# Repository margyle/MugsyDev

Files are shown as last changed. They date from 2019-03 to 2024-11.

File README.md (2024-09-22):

# Mugsy

This repo has been reset and refactored to contain a monorepo of all Mugsy services. 

🚧**This update is in progress and should not be considered complete at this time.** 🚧

You can find Mugsy's individual repos, CAD files, PCB files, and more at the official Org site on Github:  https://github.com/MugsyOS

## Applications

### Operator
Operator is a FastAPI application designed to manage and control Mugsys hardware devices. All GPIO control is handled by Operator to keep hardware related functionality isolated from the primary DECAF API, allowing for increased hardware compatibility.

Until this monorepo refactor is completed, you can find limited docs, and dev and in progress feature branches on the Org repo: https://github.com/MugsyOS/Operator



### DECAF

DECAF is Mugsy's primary REST API. It handles all the non-hardware related functionality like users, recipes, integrations and tons more. DECAF also manages the brewing process through communications with Operator.

DECAF works with Mugsy's local SQLite database, using [Better-SQLite-3](https://github.com/WiseLibs/better-sqlite3), and [Drizzle](https://orm.drizzle.team/docs/overview) for a comfy dev experience.



### JuneBug

Junebug is Mugsy's React frontend. Written in TypeScript, with some help from [Tailwind](https://tailwindcss.com/), [DaisyUI](https://daisyui.com/), [TanStack Query](https://tanstack.com/query/latest), and [Jotai](https://jotai.org/). 



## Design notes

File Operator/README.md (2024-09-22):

# Mugsy: Operator Middleware


**Please note that this app is not ready for prime time just yet and this Read Me likely out of date!**
## Introduction
This repository contains the source code for the Operator App, a FastAPI application designed to manage and control Mugsys hardware devices. All GPIO control is handled by Operator to keep hardware related functionality isolated from the primary DECAF api, allowing for increased hardware compatibility. 

Requests from the Mugsy frontend are sent to the DECAF API which handles all primary functionality. When a GPIO action is required, DECAF calls Operator to perform the action.

## Getting Started

### Prerequisites
Before you begin, ensure you have the following installed on your system:
- Python 3.8 or higher
- pip
- virtualenv (optional but recommended)

### Setting Up the Environment

To set up the project environment:
1. Clone the repository:
   ```bash
   git clone https://github.com/margyle/operator.git
   cd operator
   ```

2. Create and activate a virtual environment (optional but recommended):
   - For Unix/MacOs:
     ```bash
     python -m venv venv
     source venv/bin/activate
     ```
   - For Windows:
     ```cmd
     python -m venv venv
     venv\Scripts\activate
     ```

### Installing the Application

#### Development Mode
To install the application in editable mode, which is recommended for development purposes:
```bash
pip install -e .
```
This command allows you to modify the source code and see changes without reinstalling the package.

#### Production Mode
To install the application for production use:
```bash
pip install .
```
This command installs the application as a standard Python package.

## Usage

To start the FastAPI application, run:
```bash
uvicorn operator_app.app:app --reload --host 0.0.0.0 --port 8000
```
This command will start the FastAPI server with live reloading enabled.

## Tests

To run tests, run:
```bash
pytest
```

## Troubleshooting

If you are getting import errors, you may need to add your app source to the ENV, run:
```bash
export PYTHONPATH=$PYTHONPATH:/path/to/Operator/src
```
## Scale Setup

### Install Libraries
After testing numerous libs to handle the HX711 load cell amps, the best option was found to be the [Raspberry Pi HX711 C++ Library](https://github.com/endail/hx711) by Daniel Robertson (@endail on Github), and its associated Python wrappers for interacting with it from Operator. 

Installation: 
In order to use the Python wrapper we must first install the C++ library:
* In your terminal, enter: ```sudo apt-get install -y liblgpio-dev```
* If it is not available, manually build and install it: 

```
pi@raspberrypi:~ $ git clone --depth=1 https://github.com/endail/hx711
pi@raspberrypi:~ $ cd hx711
pi@raspberrypi:~/hx711 $ make && sudo make install
```

* Run `ldconfig` , it should not require any additional actions once completed.

Install Python Wrapper:
* ```pip3 install --upgrade hx711-rpi-py```

- - -

### Calibrate Scales (headless):
The easiest method to calibrate the scales without the UI is to start Operator and connect to the calibration endpoint in Postman: ws://mugsy-0.local:8000/v1/calibrate-scales/CONE_SCALE

> If you want to calibrate the mug platform, just swap out CONE_SCALE for MUG_SCALE in the endpoint’s URL.

Once connected, you will be walked through the calibration process. Here are the steps and the response formatting for each step: 

* Step 1: Request unit
  * Text: "Enter the unit you want to measure the object in (e.g., g, kg, lb, oz):"
  * Asking: The unit of measurement for the object. Mugsy is set up to work with grams, so enter g.
  * Expected response: ```{"unit": “g”}```
* Step 2: Request known weight
  * Text: "Enter the weight of the object in [unit]:"
  * Asking: The weight of the object you are using to calibrate the scale in grams. It currently expects a float so you should enter the weight to two decimal spots.
  * Expected response: ```{"known_weight": 100.00}```
* Step 3: Request number of samples
  * Text: "Enter the number of samples to take from the HX711 chip (e.g., 15):"
  * Asking: The number of samples to take from the HX711 chip. We have had great results with a total of 15 samples.
  * Expected response: ```{"samples": 15}```
* Step 4: Zero the scale
  * Text: "Remove all objects from the scale and then press enter."
  * Asking: Confirmation that all objects have been removed from the scale
  * Expected response: ```{“ready”: true}```
* Step 5: Measure known weight
  * Text: "Place the object on the scale and then press enter."
  * Asking: Confirmation that the object has been placed on the scale
  * Expected response: ```{“ready”: true}```
 
After these steps, the endpoint sends a final JSON response with the calibration results, including:
* known_weight
* unit
* raw_value
* samples
* reference_unit
* zero_value

The calibration values are automatically written to the hardware configuration file, ready to be used in any weight related functions.

## Contributing
Contributions to this project are welcome. Please ensure that all pull requests are well-documented and include tests where applicable.

## Third-Party Libraries

### Modified Library File

The file `src/operator_services/libs/hx711.py` in this project was based on [HX711](https://github.com/gandalf15/HX711) which is licensed under the BSD 3-Clause License, Copyright (c) 2017, Marcel Zak. Modifications were made to make it compatible with pigpio.

Original Library License: [BSD 3-Clause License](https://opensource.org/licenses/BSD-3-Clause)

Please refer to the original source for the unmodified version and further details about the library.

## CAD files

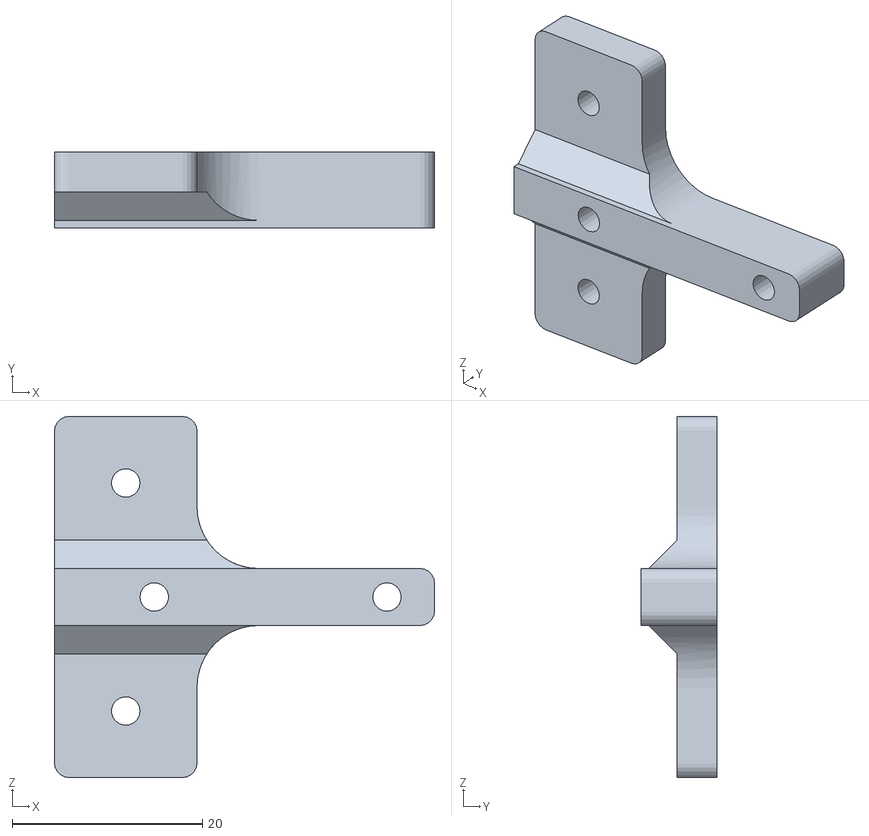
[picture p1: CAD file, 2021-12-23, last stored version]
CAD/lightbarMountRear.stl
40.0 x 8.00 x 38.0

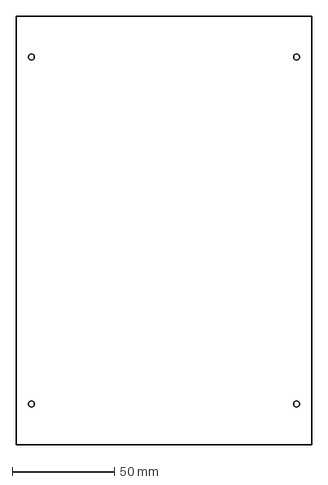
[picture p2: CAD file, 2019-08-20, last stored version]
CAD/sidePanels/mugsyBaseSidePanel_210mm.dxf
145.0 x 210.0 mm

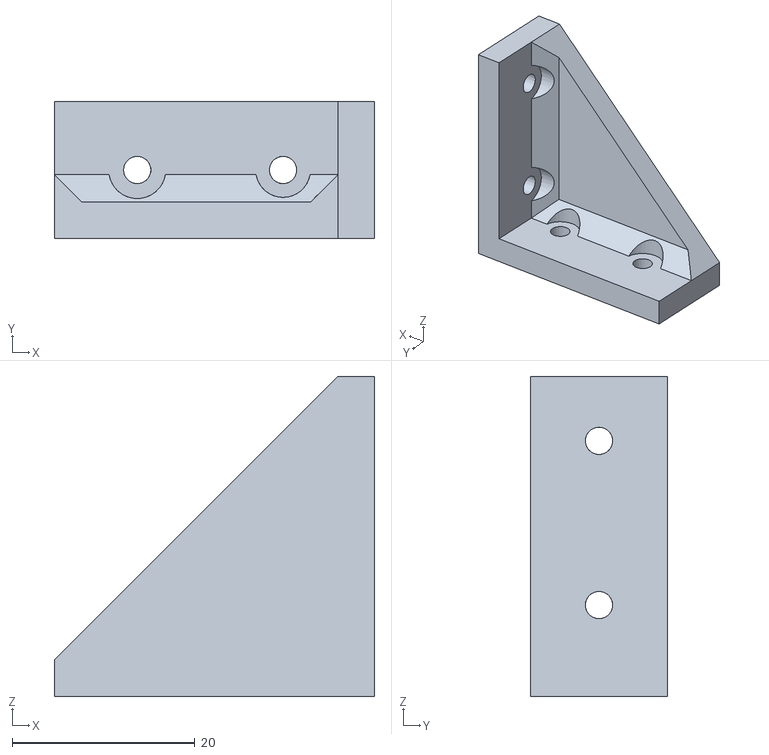
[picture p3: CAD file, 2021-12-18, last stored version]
CAD/cornerBracketV5reinforced.stl
35.0 x 15.0 x 35.0

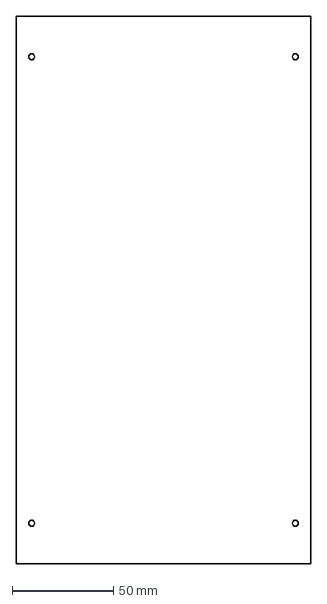
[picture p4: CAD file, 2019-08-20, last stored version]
CAD/sidePanels/mugsyBaseSidePanel_270mm.dxf
145.0 x 270.0 mm

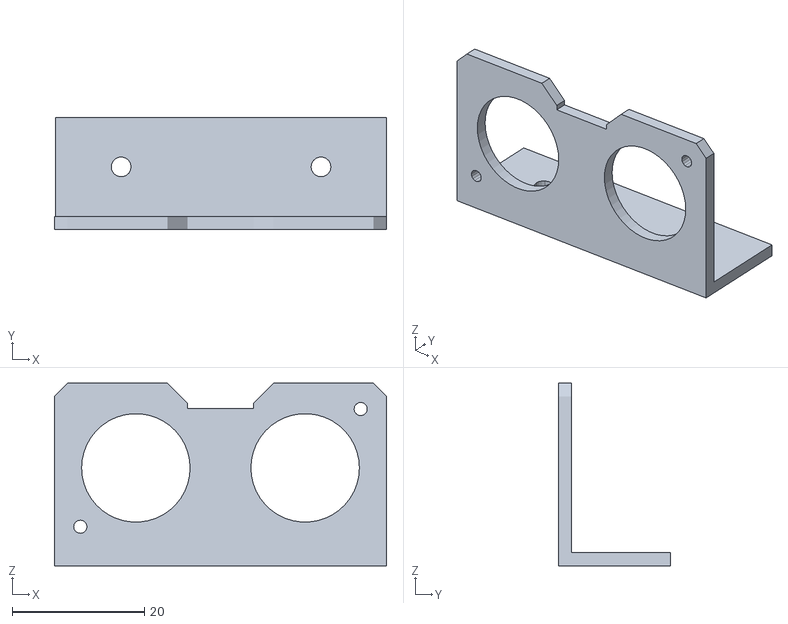
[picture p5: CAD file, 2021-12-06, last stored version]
CAD/mugSensorMount_partA.stl
50.2 x 17.0 x 27.6

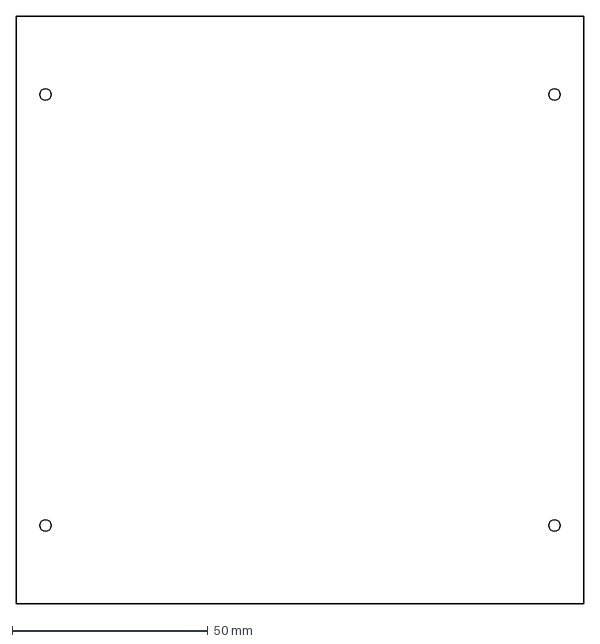
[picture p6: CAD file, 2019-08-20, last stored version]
CAD/sidePanels/mugsyBaseSidePanel.dxf
145.0 x 150.0 mm

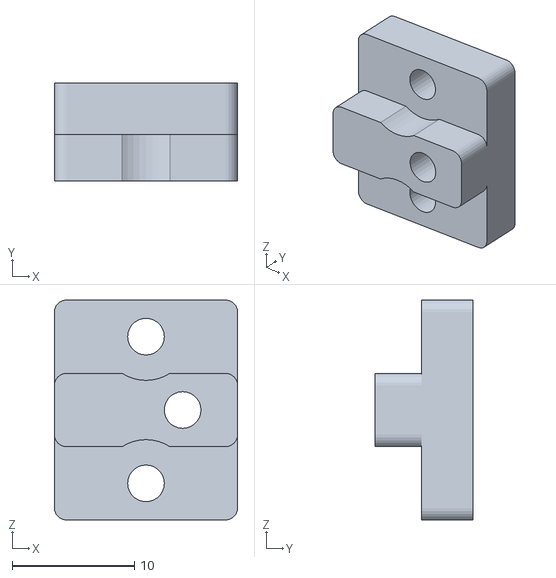
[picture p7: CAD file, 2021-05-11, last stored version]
CAD/lightBarMount_V2.stl
15.0 x 8.00 x 18.0

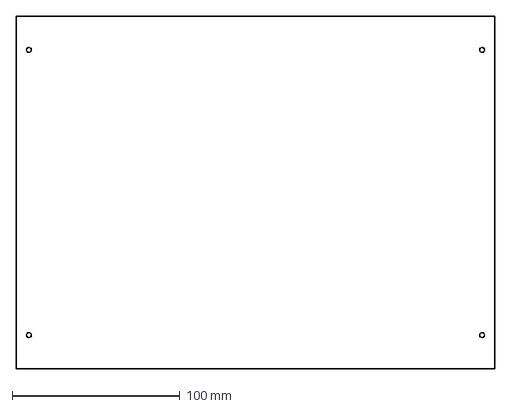
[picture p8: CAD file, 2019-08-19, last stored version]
CAD/sidePanels/mugsyHeadSidePanel.dxf
285.0 x 210.0 mm

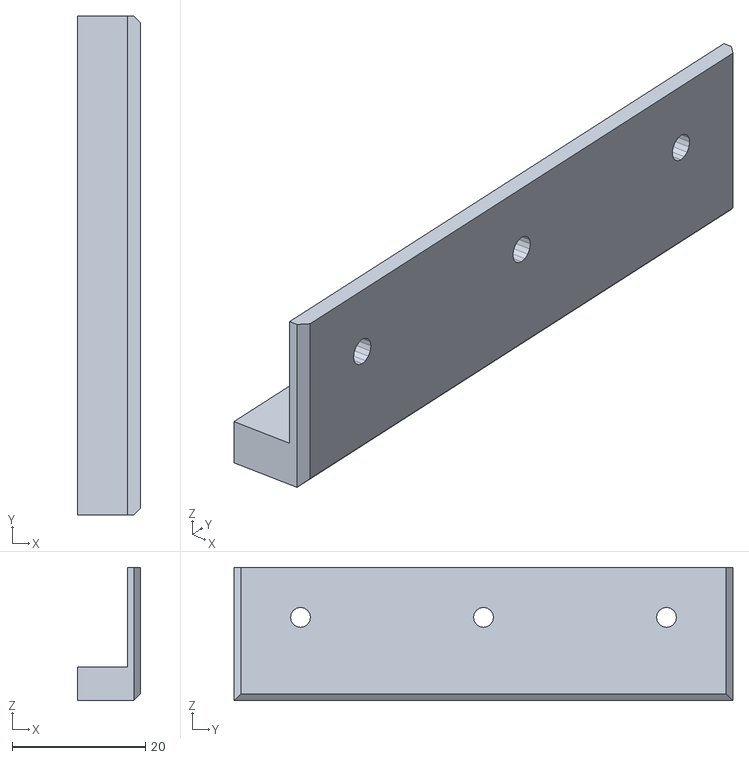
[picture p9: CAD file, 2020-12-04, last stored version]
CAD/flexBlock.stl
9.50 x 75.0 x 20.0

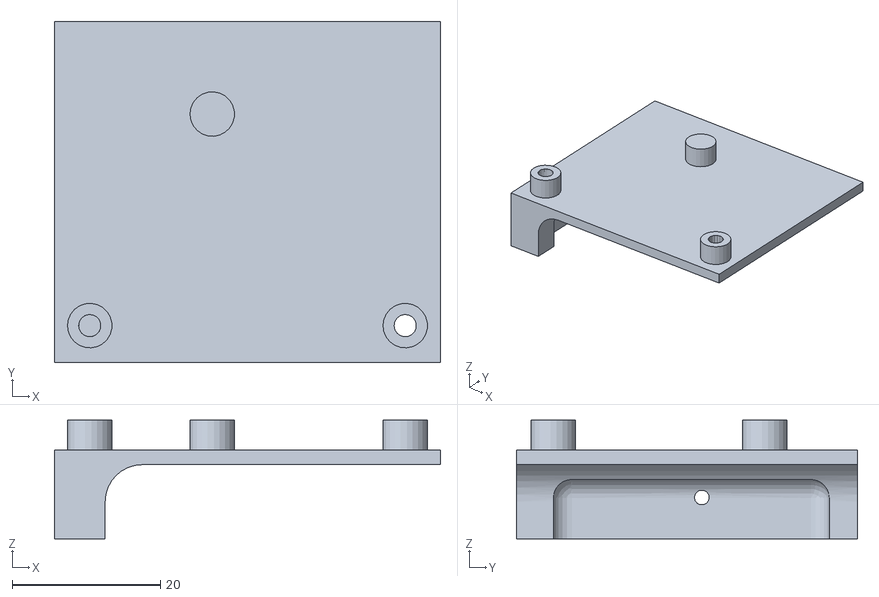
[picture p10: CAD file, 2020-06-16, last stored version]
CAD/scannerServoMount(optional).stl
52.0 x 46.0 x 16.0

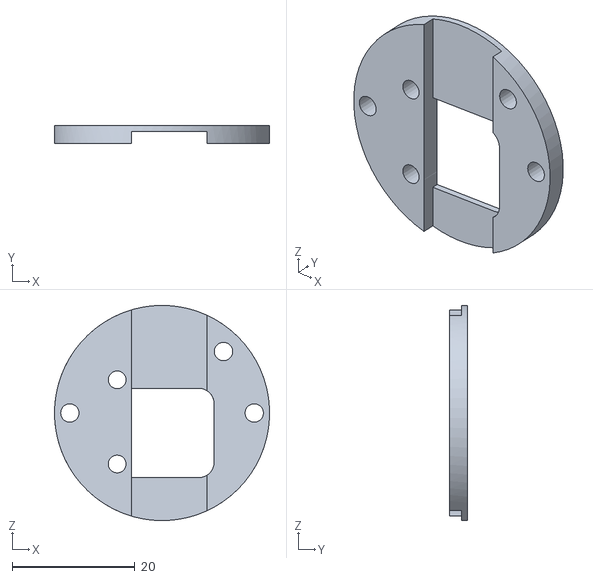
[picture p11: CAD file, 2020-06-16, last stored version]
CAD/rotaryEncoderMount.stl
35.0 x 3.00 x 35.0

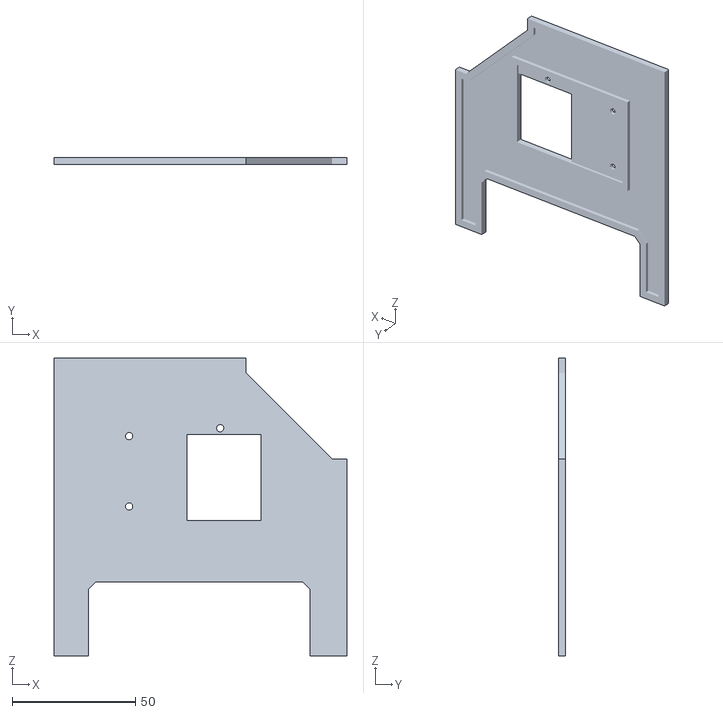
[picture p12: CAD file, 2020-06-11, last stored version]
CAD/rfidMount_V3.stl
119.0 x 3.00 x 121.0

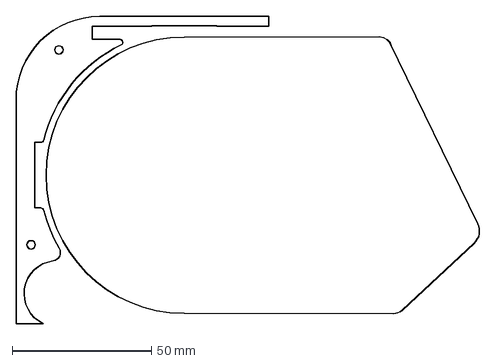
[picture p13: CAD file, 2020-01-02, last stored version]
CAD/mugsyBelt.dxf
167.0 x 110.3 mm

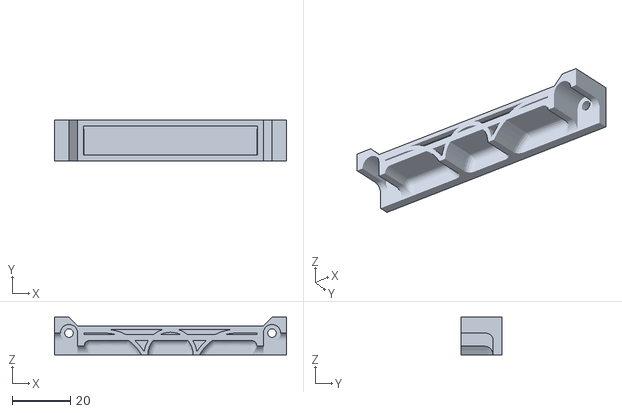
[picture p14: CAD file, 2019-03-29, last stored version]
CAD/panelMagnetMount.V4.stl
80.0 x 14.0 x 13.0

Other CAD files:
CAD/magConnPanelSide.2.stl
CAD/magConnLid.2.stl
CAD/magConnMachineSide.2.stl
CAD/plugCap.stl
CAD/PouroverMidSection.stl
CAD/barcodeScanMount.stl
CAD/behindScreenDividerLaser.dxf
CAD/coneMechGear.stl
CAD/coneMechGearTop.stl
CAD/coneMechMid.stl
CAD/controllerPlates.stl
CAD/controllerPlatesLaser.dxf
CAD/grinderGear.stl
CAD/grinderSpoutMountV2.stl
CAD/grinderSpoutV2.stl
CAD/pourOverMechTop.dxf
CAD/pourOverMount.stl
CAD/rgbLedMount.stl
CAD/screenClipV2.stl
CAD/sweepServoMount.stl
CAD/waterSweepV1.stl

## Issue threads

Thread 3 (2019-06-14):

nonBlockingSerialStepper.ino broke command chaining

margyle, 2019-06-14:
Move to non-blocking motor controller introduced some bugs.  Most important one being command chaining. Fix in progress.

margyle, 2019-06-14:
Fixed the command chaining bug. Just need to reintegrate the water pump control, come clean up and we are good to go.

Closed 2019-06-22.

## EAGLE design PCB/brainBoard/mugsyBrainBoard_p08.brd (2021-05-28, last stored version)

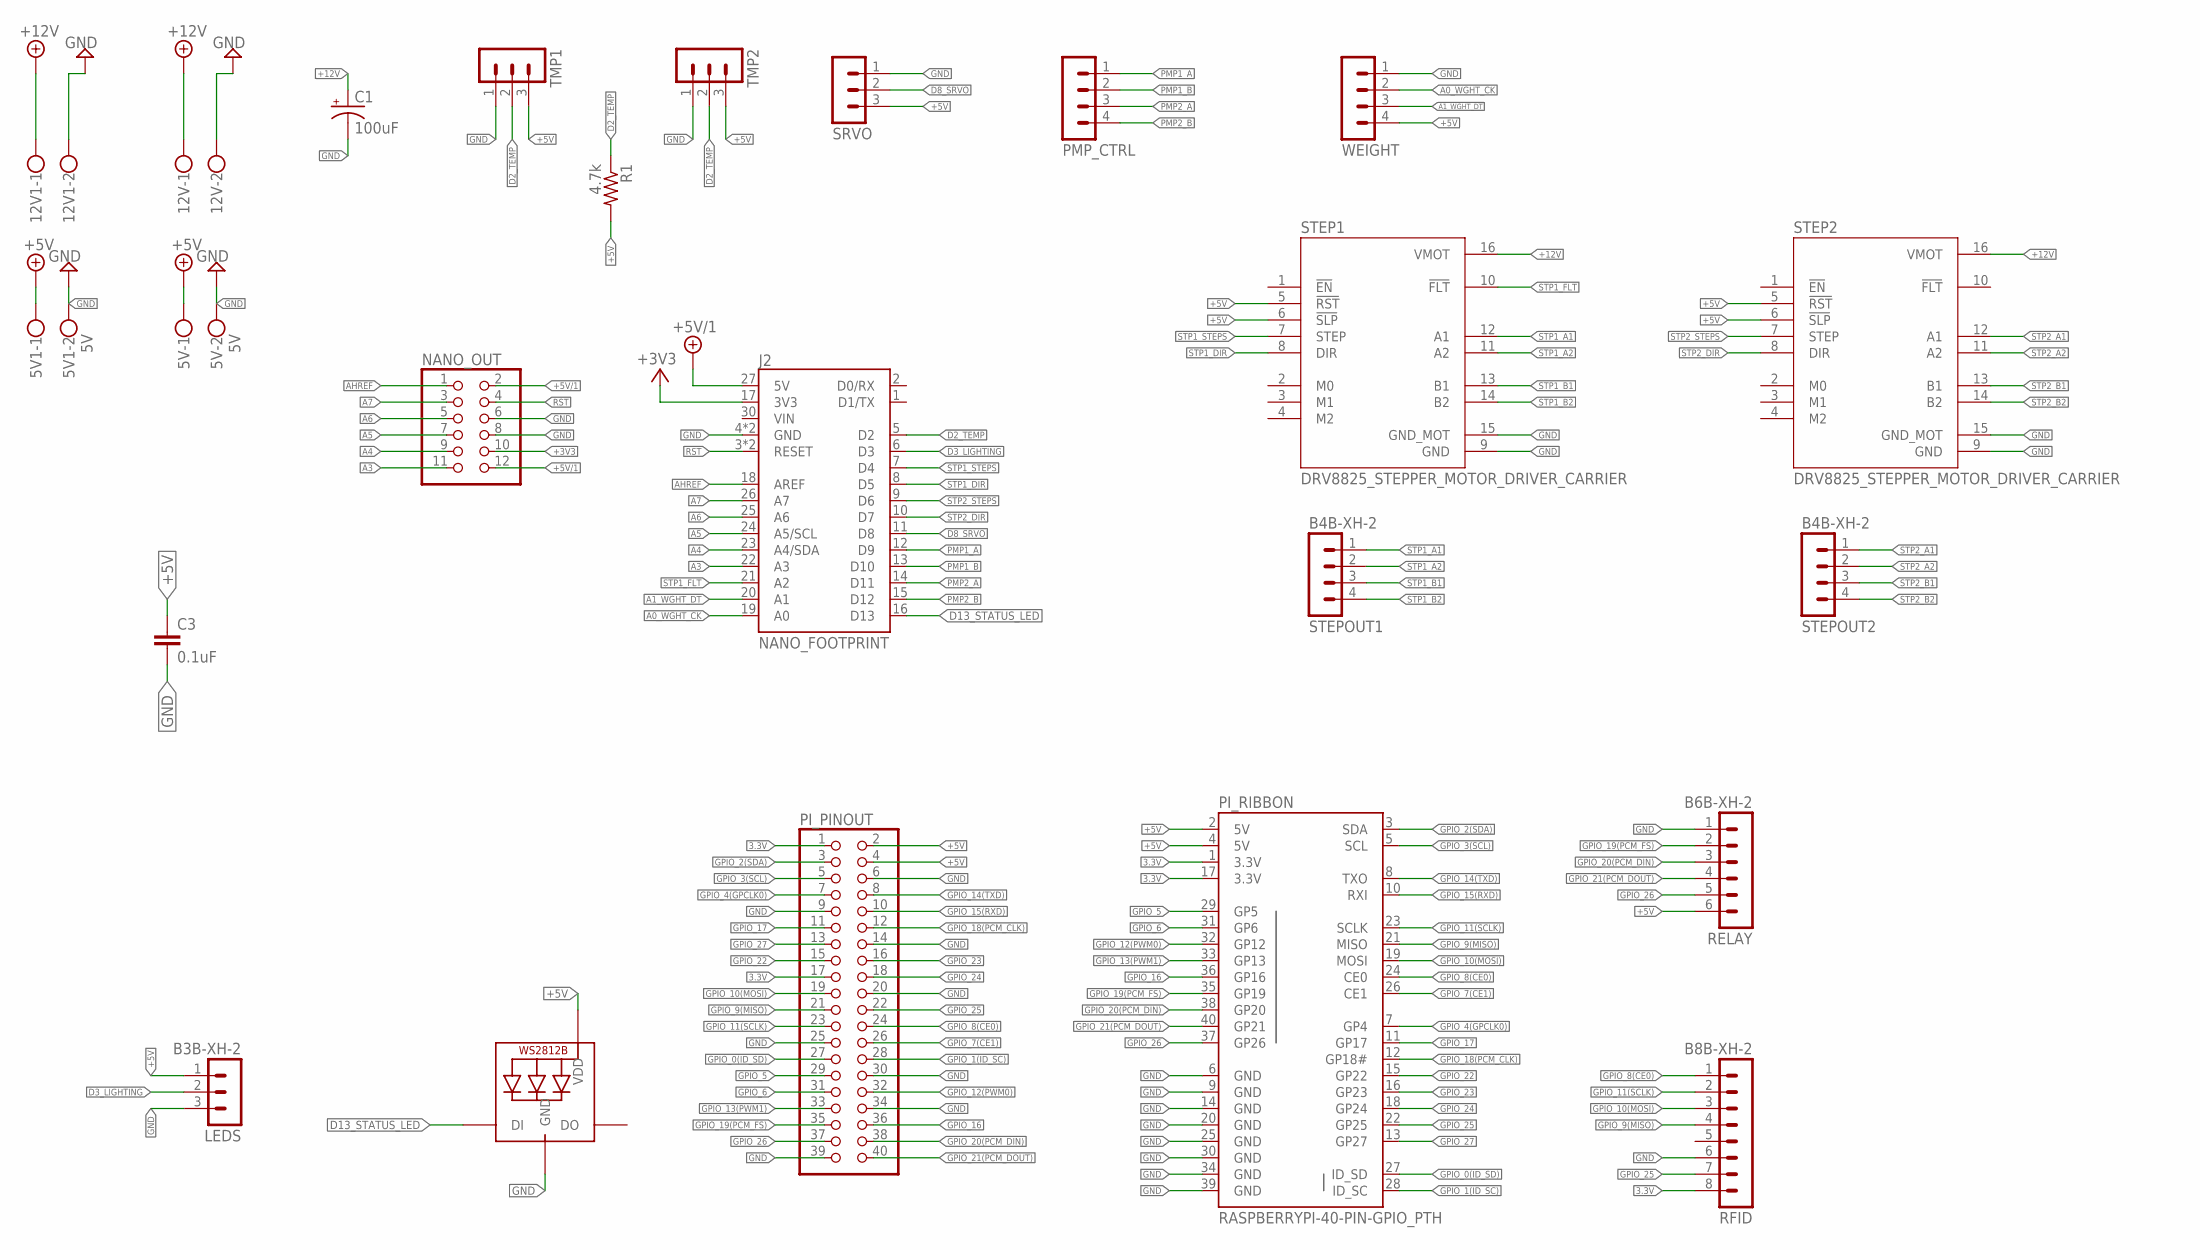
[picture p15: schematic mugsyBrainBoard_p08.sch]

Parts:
5V, 5V1: 5V; W237-102
12V, 12V1: W237-102
C1: 100uF; CPOL-RADIAL-2.5MM-6.5MM
C3: 0.1uF; C050-030X075
J2: NANO_FOOTPRINT; NANO
LEDS: B3B-XH-2; B3B-XH-A
NANO_OUT: PINHD-2X6; 2X06
PI_PINOUT: PINHD-2X20; 2X20
PI_RIBBON: RASPBERRYPI-40-PIN-GPIO_PTH; 2X20_SHROUDED
PMP_CTRL: B4B-XH-2; B4B-XH-A
R1: 4.7k; 0207/5V
RELAY: B6B-XH-2; B6B-XH-A
RFID: B8B-XH-2; B8B-XH-A
SRVO: B3B-XH-2; B3B-XH-A
STATUS: WS2812B5050; WS2812B
STEP1, STEP2: DRV8825_STEPPER_MOTOR_DRIVER_CARRIER; IC_DRV8825_STEPPER_MOTOR_DRIVER_CARRIER
STEPOUT1, STEPOUT2: B4B-XH-2; B4B-XH-A
TMP1, TMP2: B3B-XH-2; B3B-XH-A
WEIGHT: B4B-XH-2; B4B-XH-A

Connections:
3.3V: PI_PINOUT.1, PI_PINOUT.17, PI_RIBBON.1 (3.3V), PI_RIBBON.17 (3.3V), RFID.8
+3V3: J2.17 (3V3), NANO_OUT.10
+5V: 5V.1, 5V1.1, C3.1, LEDS.1, PI_PINOUT.2, PI_PINOUT.4, PI_RIBBON.2 (5V), PI_RIBBON.4 (5V), R1.2, RELAY.6, SRVO.3, STATUS.1-VDD (VDD), STEP1.5 (!RST), STEP1.6 (!SLP), STEP2.5 (!RST), STEP2.6 (!SLP), TMP1.3, TMP2.3, WEIGHT.4
+5V/1: J2.27 (5V), NANO_OUT.2, NANO_OUT.12
+12V: 12V.1, 12V1.1, C1.1 (+), STEP1.16 (VMOT), STEP2.16 (VMOT)
A0_WGHT_CK: J2.19 (A0), WEIGHT.2
A1_WGHT_DT: J2.20 (A1), WEIGHT.3
A3: J2.22 (A3), NANO_OUT.11
A4: J2.23 (A4/SDA), NANO_OUT.9
A5: J2.24 (A5/SCL), NANO_OUT.7
A6: J2.25 (A6), NANO_OUT.5
A7: J2.26 (A7), NANO_OUT.3
AHREF: J2.18 (AREF), NANO_OUT.1
D2_TEMP: J2.5 (D2), R1.1, TMP1.2, TMP2.2
D3_LIGHTING: J2.6 (D3), LEDS.2
D8_SRVO: J2.11 (D8), SRVO.2
D13_STATUS_LED: J2.16 (D13), STATUS.4-DIN (DI)
GND: 5V.2, 5V1.2, 12V.2, 12V1.2, C1.2 (-), C3.2, J2.4 (GND), J2.29 (GND), LEDS.3, NANO_OUT.6, NANO_OUT.8, PI_PINOUT.6, PI_PINOUT.9, PI_PINOUT.14, PI_PINOUT.20, PI_PINOUT.25, PI_PINOUT.30, PI_PINOUT.34, PI_PINOUT.39, PI_RIBBON.6 (GND), PI_RIBBON.9 (GND), PI_RIBBON.14 (GND), PI_RIBBON.20 (GND), PI_RIBBON.25 (GND), PI_RIBBON.30 (GND), PI_RIBBON.34 (GND), PI_RIBBON.39 (GND), RELAY.1, RFID.6, SRVO.1, STATUS.3-GND (GND), STEP1.9 (GND), STEP1.15 (GND_MOT), STEP2.9 (GND), STEP2.15 (GND_MOT), TMP1.1, TMP2.1, WEIGHT.1
GPIO_0(ID_SD): PI_PINOUT.27, PI_RIBBON.27 (ID_SD)
GPIO_1(ID_SC): PI_PINOUT.28, PI_RIBBON.28 (ID_SC)
GPIO_2(SDA): PI_PINOUT.3, PI_RIBBON.3 (SDA)
GPIO_3(SCL): PI_PINOUT.5, PI_RIBBON.5 (SCL)
GPIO_4(GPCLK0): PI_PINOUT.7, PI_RIBBON.7 (GP4)
GPIO_5: PI_PINOUT.29, PI_RIBBON.29 (GP5)
GPIO_6: PI_PINOUT.31, PI_RIBBON.31 (GP6)
GPIO_7(CE1): PI_PINOUT.26, PI_RIBBON.26 (CE1)
GPIO_8(CE0): PI_PINOUT.24, PI_RIBBON.24 (CE0), RFID.1
GPIO_9(MISO): PI_PINOUT.21, PI_RIBBON.21 (MISO), RFID.4
GPIO_10(MOSI): PI_PINOUT.19, PI_RIBBON.19 (MOSI), RFID.3
GPIO_11(SCLK): PI_PINOUT.23, PI_RIBBON.23 (SCLK), RFID.2
GPIO_12(PWM0): PI_PINOUT.32, PI_RIBBON.32 (GP12)
GPIO_13(PWM1): PI_PINOUT.33, PI_RIBBON.33 (GP13)
GPIO_14(TXD): PI_PINOUT.8, PI_RIBBON.8 (TXO)
GPIO_15(RXD): PI_PINOUT.10, PI_RIBBON.10 (RXI)
GPIO_16: PI_PINOUT.36, PI_RIBBON.36 (GP16)
GPIO_17: PI_PINOUT.11, PI_RIBBON.11 (GP17)
GPIO_18(PCM_CLK): PI_PINOUT.12, PI_RIBBON.12 (GP18#)
GPIO_19(PCM_FS): PI_PINOUT.35, PI_RIBBON.35 (GP19), RELAY.2
GPIO_20(PCM_DIN): PI_PINOUT.38, PI_RIBBON.38 (GP20), RELAY.3
GPIO_21(PCM_DOUT): PI_PINOUT.40, PI_RIBBON.40 (GP21), RELAY.4
GPIO_22: PI_PINOUT.15, PI_RIBBON.15 (GP22)
GPIO_23: PI_PINOUT.16, PI_RIBBON.16 (GP23)
GPIO_24: PI_PINOUT.18, PI_RIBBON.18 (GP24)
GPIO_25: PI_PINOUT.22, PI_RIBBON.22 (GP25), RFID.7
GPIO_26: PI_PINOUT.37, PI_RIBBON.37 (GP26), RELAY.5
GPIO_27: PI_PINOUT.13, PI_RIBBON.13 (GP27)
PMP1_A: J2.12 (D9), PMP_CTRL.1
PMP1_B: J2.13 (D10), PMP_CTRL.2
PMP2_A: J2.14 (D11), PMP_CTRL.3
PMP2_B: J2.15 (D12), PMP_CTRL.4
RST: J2.3 (RESET), J2.28 (RESET), NANO_OUT.4
STP1_A1: STEP1.12 (A1), STEPOUT1.1
STP1_A2: STEP1.11 (A2), STEPOUT1.2
STP1_B1: STEP1.13 (B1), STEPOUT1.3
STP1_B2: STEP1.14 (B2), STEPOUT1.4
STP1_DIR: J2.8 (D5), STEP1.8 (DIR)
STP1_FLT: J2.21 (A2), STEP1.10 (!FLT)
STP1_STEPS: J2.7 (D4), STEP1.7 (STEP)
STP2_A1: STEP2.12 (A1), STEPOUT2.1
STP2_A2: STEP2.11 (A2), STEPOUT2.2
STP2_B1: STEP2.13 (B1), STEPOUT2.3
STP2_B2: STEP2.14 (B2), STEPOUT2.4
STP2_DIR: J2.10 (D7), STEP2.8 (DIR)
STP2_STEPS: J2.9 (D6), STEP2.7 (STEP)

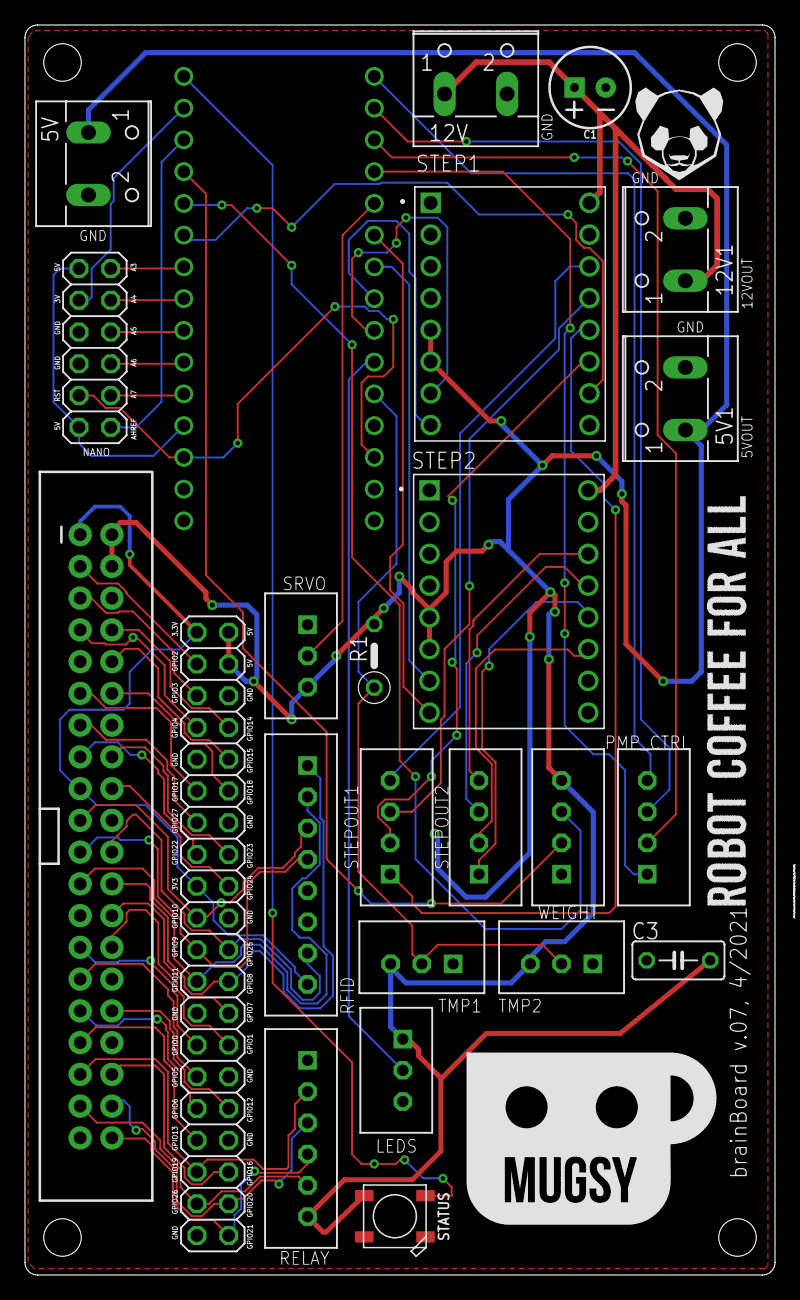
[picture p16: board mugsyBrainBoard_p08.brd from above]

Board: 2 copper layers, 60.0 x 100.0 mm, 24 parts (0 on the bottom side), 64 nets.

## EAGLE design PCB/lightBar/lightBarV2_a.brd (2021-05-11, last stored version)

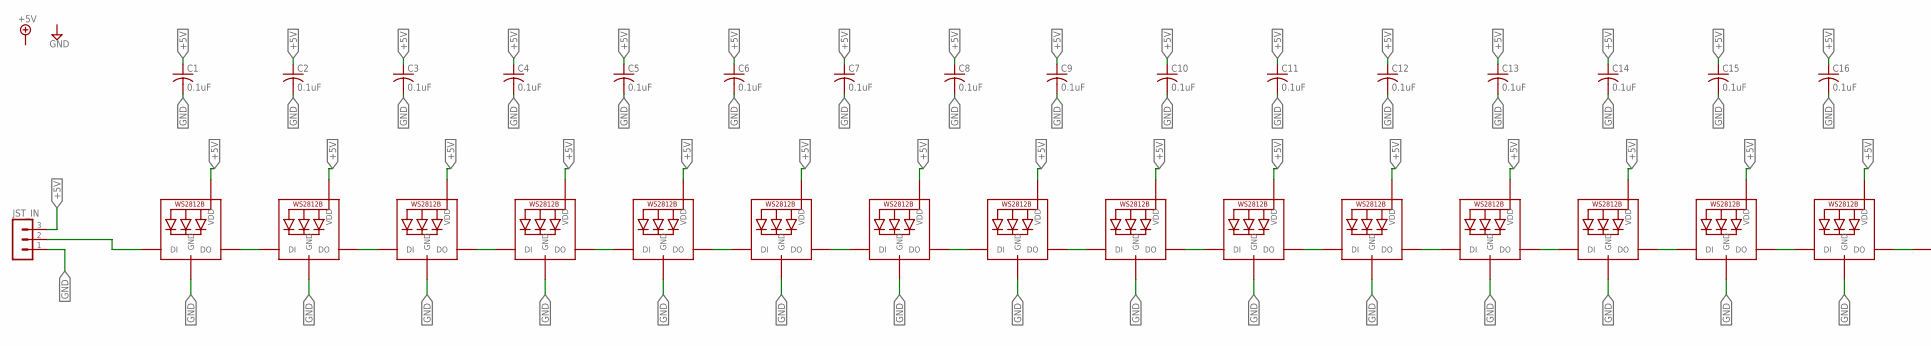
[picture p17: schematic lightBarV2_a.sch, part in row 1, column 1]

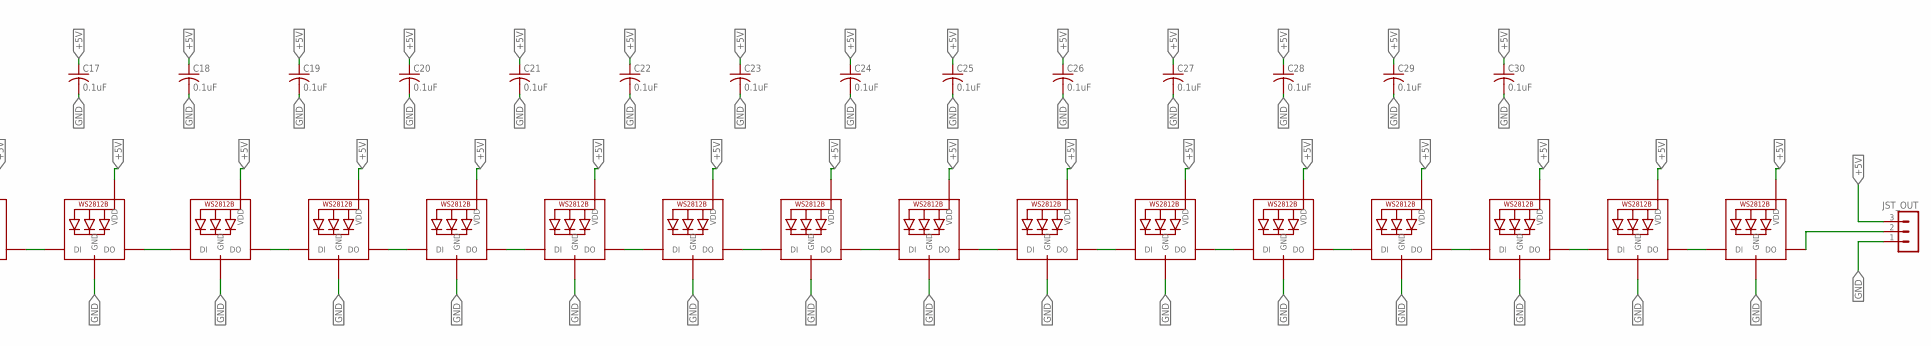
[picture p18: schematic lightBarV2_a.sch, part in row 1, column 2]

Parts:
C1, C2, C3, C4, C5, C6, C7, C8, C9, C10, C11, C12, C13, C14, C15, C16, C17, C18, C19, C20, C21, C22, C23, C24, C25, C26, C27, C28, C29, C30: 0.1uF; C0805K
JST_IN: B3B-XH-2; B3B-XH-A
JST_OUT: B3B-XH-2; B3B-XH-A
LED1, LED2, LED3, LED4, LED5, LED6, LED7, LED8, LED9, LED10, LED11, LED12, LED13, LED14, LED15, LED16, LED17, LED18, LED19, LED20, LED21, LED22, LED23, LED24, LED25, LED26, LED27, LED28, LED29, LED30: WS2812B5050; WS2812B

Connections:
+5V: C1.1, C2.1, C3.1, C4.1, C5.1, C6.1, C7.1, C8.1, C9.1, C10.1, C11.1, C12.1, C13.1, C14.1, C15.1, C16.1, C17.1, C18.1, C19.1, C20.1, C21.1, C22.1, C23.1, C24.1, C25.1, C26.1, C27.1, C28.1, C29.1, C30.1, JST_IN.3, JST_OUT.3, LED1.1-VDD (VDD), LED2.1-VDD (VDD), LED3.1-VDD (VDD), LED4.1-VDD (VDD), LED5.1-VDD (VDD), LED6.1-VDD (VDD), LED7.1-VDD (VDD), LED8.1-VDD (VDD), LED9.1-VDD (VDD), LED10.1-VDD (VDD), LED11.1-VDD (VDD), LED12.1-VDD (VDD), LED13.1-VDD (VDD), LED14.1-VDD (VDD), LED15.1-VDD (VDD), LED16.1-VDD (VDD), LED17.1-VDD (VDD), LED18.1-VDD (VDD), LED19.1-VDD (VDD), LED20.1-VDD (VDD), LED21.1-VDD (VDD), LED22.1-VDD (VDD), LED23.1-VDD (VDD), LED24.1-VDD (VDD), LED25.1-VDD (VDD), LED26.1-VDD (VDD), LED27.1-VDD (VDD), LED28.1-VDD (VDD), LED29.1-VDD (VDD), LED30.1-VDD (VDD)
GND: C1.2, C2.2, C3.2, C4.2, C5.2, C6.2, C7.2, C8.2, C9.2, C10.2, C11.2, C12.2, C13.2, C14.2, C15.2, C16.2, C17.2, C18.2, C19.2, C20.2, C21.2, C22.2, C23.2, C24.2, C25.2, C26.2, C27.2, C28.2, C29.2, C30.2, JST_IN.1, JST_OUT.1, LED1.3-GND (GND), LED2.3-GND (GND), LED3.3-GND (GND), LED4.3-GND (GND), LED5.3-GND (GND), LED6.3-GND (GND), LED7.3-GND (GND), LED8.3-GND (GND), LED9.3-GND (GND), LED10.3-GND (GND), LED11.3-GND (GND), LED12.3-GND (GND), LED13.3-GND (GND), LED14.3-GND (GND), LED15.3-GND (GND), LED16.3-GND (GND), LED17.3-GND (GND), LED18.3-GND (GND), LED19.3-GND (GND), LED20.3-GND (GND), LED21.3-GND (GND), LED22.3-GND (GND), LED23.3-GND (GND), LED24.3-GND (GND), LED25.3-GND (GND), LED26.3-GND (GND), LED27.3-GND (GND), LED28.3-GND (GND), LED29.3-GND (GND), LED30.3-GND (GND)
unnamed: LED29.2-DOUT (DO), LED30.4-DIN (DI)
unnamed: LED28.2-DOUT (DO), LED29.4-DIN (DI)
unnamed: LED27.2-DOUT (DO), LED28.4-DIN (DI)
unnamed: LED26.2-DOUT (DO), LED27.4-DIN (DI)
unnamed: LED25.2-DOUT (DO), LED26.4-DIN (DI)
unnamed: LED24.2-DOUT (DO), LED25.4-DIN (DI)
unnamed: LED23.2-DOUT (DO), LED24.4-DIN (DI)
unnamed: LED22.2-DOUT (DO), LED23.4-DIN (DI)
unnamed: LED21.2-DOUT (DO), LED22.4-DIN (DI)
unnamed: LED20.2-DOUT (DO), LED21.4-DIN (DI)
unnamed: LED19.2-DOUT (DO), LED20.4-DIN (DI)
unnamed: LED18.2-DOUT (DO), LED19.4-DIN (DI)
unnamed: LED17.2-DOUT (DO), LED18.4-DIN (DI)
unnamed: LED16.2-DOUT (DO), LED17.4-DIN (DI)
unnamed: LED15.2-DOUT (DO), LED16.4-DIN (DI)
unnamed: LED14.2-DOUT (DO), LED15.4-DIN (DI)
unnamed: LED13.2-DOUT (DO), LED14.4-DIN (DI)
unnamed: LED12.2-DOUT (DO), LED13.4-DIN (DI)
unnamed: LED11.2-DOUT (DO), LED12.4-DIN (DI)
unnamed: LED10.2-DOUT (DO), LED11.4-DIN (DI)
unnamed: LED9.2-DOUT (DO), LED10.4-DIN (DI)
unnamed: LED8.2-DOUT (DO), LED9.4-DIN (DI)
unnamed: LED7.2-DOUT (DO), LED8.4-DIN (DI)
unnamed: LED6.2-DOUT (DO), LED7.4-DIN (DI)
unnamed: LED5.2-DOUT (DO), LED6.4-DIN (DI)
unnamed: LED4.2-DOUT (DO), LED5.4-DIN (DI)
unnamed: LED3.2-DOUT (DO), LED4.4-DIN (DI)
unnamed: LED1.2-DOUT (DO), LED2.4-DIN (DI)
unnamed: LED2.2-DOUT (DO), LED3.4-DIN (DI)
unnamed: JST_IN.2, LED1.4-DIN (DI)
unnamed: JST_OUT.2, LED30.2-DOUT (DO)

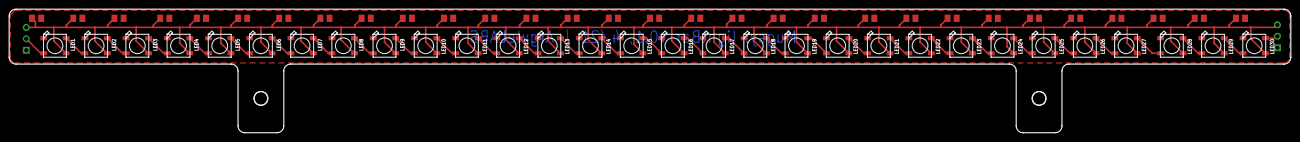
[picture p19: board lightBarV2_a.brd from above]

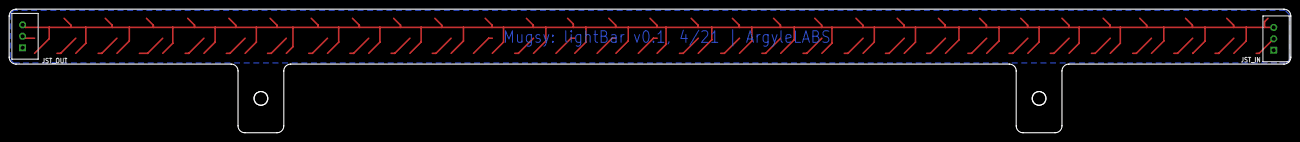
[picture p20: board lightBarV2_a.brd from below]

Board: 2 copper layers, 280.0 x 27.0 mm, 62 parts (2 on the bottom side), 33 nets.

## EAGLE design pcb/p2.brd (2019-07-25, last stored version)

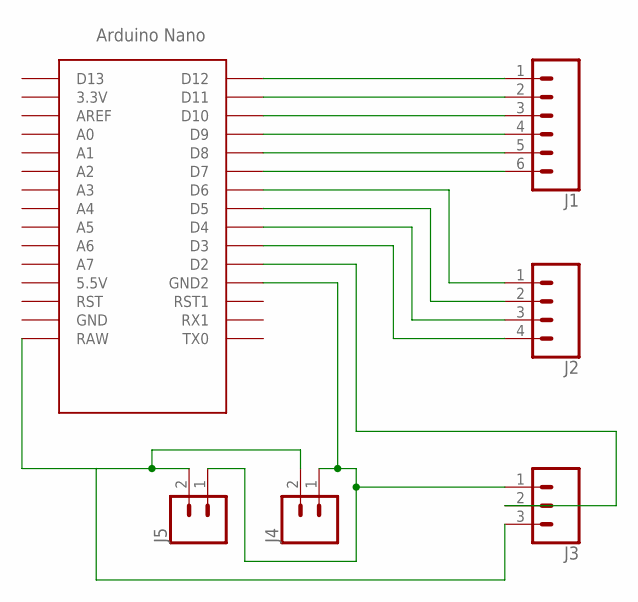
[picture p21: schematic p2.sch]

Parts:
J1: CONN_06LONGPADS; 1X06_LONGPADS
J2: CONN_04LONGPADS; 1X04_LONGPADS
J3: CONN_03LONGPADS; 1X03_LONGPADS
J4, J5: CONN_02PTH3; 1X02_LONGPADS
U$1: NANO

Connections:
unnamed: J1.1, U$1.D12
unnamed: J1.2, U$1.D11
unnamed: J1.3, U$1.D10
unnamed: J1.4, U$1.D9
unnamed: J1.5, U$1.D8
unnamed: J1.6, U$1.D7
unnamed: J2.1, U$1.D6
unnamed: J2.2, U$1.D5
unnamed: J2.3, U$1.D4
unnamed: J2.4, U$1.D3
unnamed: J3.2, U$1.D2
unnamed: J3.3, J4.2, J5.2, U$1.RAW
unnamed: J3.1, J4.1, J5.1, U$1.GND1 (GND2)

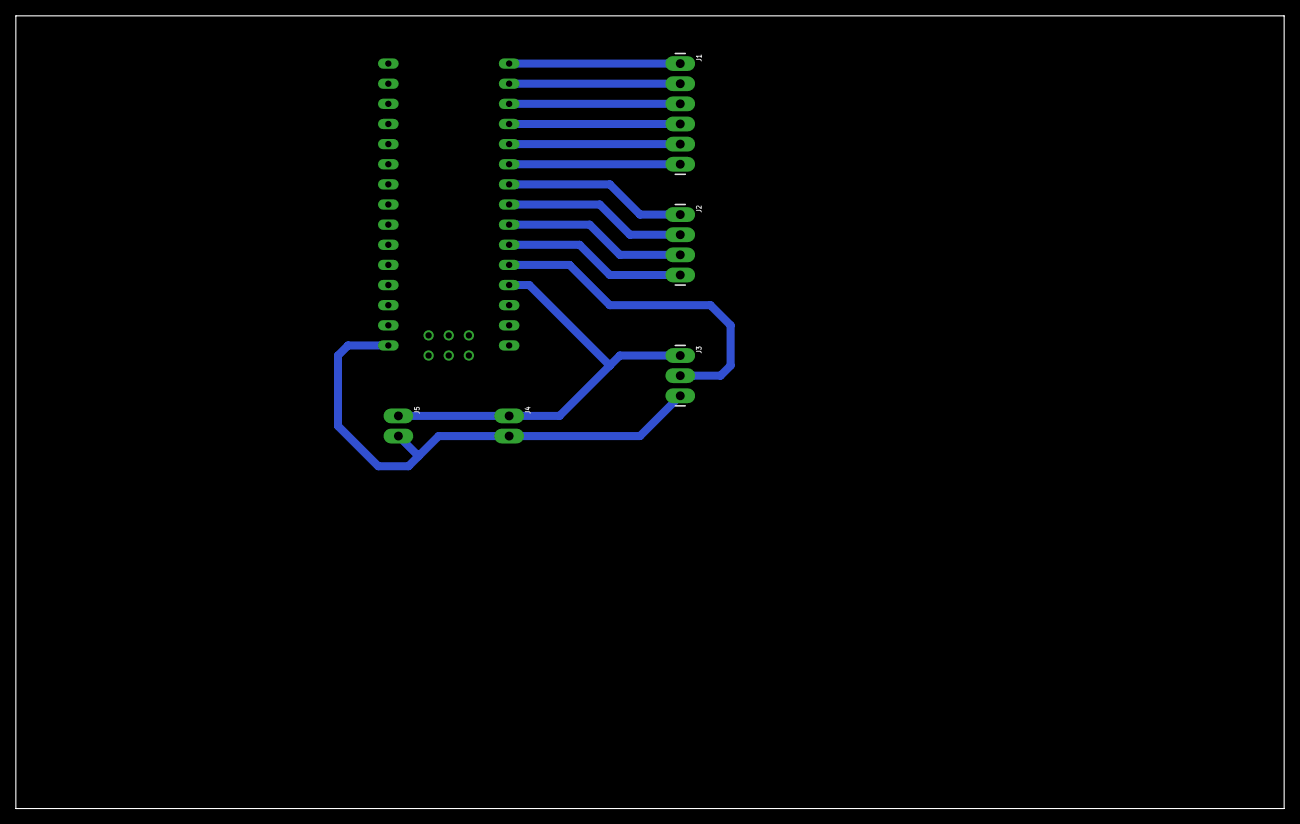
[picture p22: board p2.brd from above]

Board: 2 copper layers, 160.0 x 100.0 mm, 6 parts (0 on the bottom side), 13 nets.

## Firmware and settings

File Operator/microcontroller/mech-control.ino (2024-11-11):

#include <CmdMessenger.h>
#include <AccelStepper.h>

// Stepper definitions
#define CONE_STEP_PIN 3
#define CONE_DIR_PIN 2
#define CONE_ENABLE_PIN 4
#define SPOUT_STEP_PIN 6
#define SPOUT_DIR_PIN 5
#define SPOUT_ENABLE_PIN 7

// Microstepping pins
#define M0 11
#define M1 10
#define M2 9

// Limit switch pin
#define LIMIT_SWITCH_PIN 8

AccelStepper coneStepper(AccelStepper::DRIVER, CONE_STEP_PIN, CONE_DIR_PIN);
AccelStepper spoutStepper(AccelStepper::DRIVER, SPOUT_STEP_PIN, SPOUT_DIR_PIN);

const float STEP_ANGLE = 0.9;            // Step angle in degrees
const int MICROSTEPS = 32;               // Microsteps
const float PULLEY_RATIO = 40.0 / 20.0;  // Pulley ratio
const float SPOUT_STEPS_PER_DEGREE = (1.0 / STEP_ANGLE) * MICROSTEPS * PULLEY_RATIO;

// Track zeroing state
bool isZeroed = false;

// Command IDs
enum {
    move_cone,
    cone_done,
    move_spout,
    spout_done,
    move_both,
    both_done,
    zero_spout,  // New command
    zero_done,   // New acknowledgment
    error
};

// Command queue structure
struct Command {
    int commandId;
    long coneSteps;
    long spoutDegrees;
    int coneSpeed;
    int spoutSpeed;
    int direction;
    bool needsAck;
};

Command commandQueue[20];
int queueFront = 0;
int queueRear = 0;

bool isQueueEmpty() {
    return queueFront == queueRear;
}

bool isQueueFull() {
    return (queueRear + 1) % 20 == queueFront;
}

void enqueueCommand(Command cmd) {
    if (!isQueueFull()) {
        commandQueue[queueRear] = cmd;
        queueRear = (queueRear + 1) % 20;
    }
}

Command dequeueCommand() {
    Command cmd = commandQueue[queueFront];
    queueFront = (queueFront + 1) % 20;
    return cmd;
}

// CmdMessenger setup
CmdMessenger c = CmdMessenger(Serial, ',', ';', '/');

void on_zero_spout(void) {
    if (isQueueFull()) {
        c.sendCmd(error, "Queue full");
        return;
    }
    Command cmd = {zero_spout, 0, 0, 0, 0, 0, true};
    enqueueCommand(cmd);
}

void on_move_cone(void) {
    if (isQueueFull()) {
        c.sendCmd(error, "Queue full");
        return;
    }
    long steps = c.readBinArg<long>();
    int speed = c.readBinArg<int>();
    int direction = c.readBinArg<int>();
    Command cmd = {move_cone, steps, 0, speed, 0, direction, true};
    enqueueCommand(cmd);
}

void on_move_spout(void) {
    if (isQueueFull()) {
        c.sendCmd(error, "Queue full");
        return;
    }
    if (!isZeroed) {
        c.sendCmd(error, "Spout not zeroed");
        return;
    }
    long degrees = c.readBinArg<long>();
    int speed = c.readBinArg<int>();
    int direction = c.readBinArg<int>();
    Command cmd = {move_spout, 0, degrees, 0, speed, direction, true};
    enqueueCommand(cmd);
}

void on_move_both(void) {
    if (isQueueFull()) {
        c.sendCmd(error, "Queue full");
        return;
    }
    if (!isZeroed) {
        c.sendCmd(error, "Spout not zeroed");
        return;
    }
    long coneSteps = c.readBinArg<long>();
    int coneSpeed = c.readBinArg<int>();
    long spoutDegrees = c.readBinArg<long>();
    int spoutSpeed = c.readBinArg<int>();
    int direction = c.readBinArg<int>();
    Command cmd = {move_both, coneSteps, spoutDegrees, coneSpeed, spoutSpeed, direction, true};
    enqueueCommand(cmd);
}

void executeCommand(Command cmd) {
    switch (cmd.commandId) {
        case zero_spout:
            zeroSpoutStepper();
            if (cmd.needsAck) {
                c.sendCmd(zero_done);
            }
            break;

        case move_cone:
            coneStepper.setMaxSpeed(abs(cmd.coneSpeed));
            coneStepper.setPinsInverted(cmd.direction == 1, false, true);
            coneStepper.move(cmd.coneSteps);
            if (cmd.needsAck) {
                c.sendCmd(cone_done);
            }
            break;

        case move_spout:
            spoutStepper.setMaxSpeed(abs(cmd.spoutSpeed));
            spoutStepper.setPinsInverted(cmd.direction == 1, false, true);
            spoutStepper.moveTo(cmd.spoutDegrees * SPOUT_STEPS_PER_DEGREE);
            if (cmd.needsAck) {
                c.sendCmd(spout_done);
            }
            break;

        case move_both:
            coneStepper.setMaxSpeed(abs(cmd.coneSpeed));
            spoutStepper.setMaxSpeed(abs(cmd.spoutSpeed));
            coneStepper.setPinsInverted(cmd.direction == 1, false, true);
            spoutStepper.setPinsInverted(cmd.direction == 1, false, true);
            coneStepper.move(cmd.coneSteps);
            spoutStepper.moveTo(cmd.spoutDegrees * SPOUT_STEPS_PER_DEGREE);
            if (cmd.needsAck) {
                c.sendCmd(both_done);
            }
            break;
    }
}

void zeroSpoutStepper() {
    // Enable the motor
    digitalWrite(SPOUT_ENABLE_PIN, LOW);
    spoutStepper.setSpeed(-3000);
    
    while (digitalRead(LIMIT_SWITCH_PIN) == LOW) {
        spoutStepper.runSpeed();
    }

    // Test movement
    long stepsToMove = (long)(44 * SPOUT_STEPS_PER_DEGREE);
    spoutStepper.move(stepsToMove);
    while (spoutStepper.distanceToGo() != 0) {
        spoutStepper.run();
    }

    spoutStepper.setCurrentPosition(0);
    isZeroed = true;
    spoutStepper.disableOutputs();
}

void attach_callbacks(void) {
    c.attach(move_cone, on_move_cone);
    c.attach(move_spout, on_move_spout);
    c.attach(move_both, on_move_both);
    c.attach(zero_spout, on_zero_spout);  // Add this line
}

void setup() {
    Serial.begin(9600);

    // Set up the microstepping pins as outputs and configure for 1/32 microstepping
    pinMode(M0, OUTPUT);
    pinMode(M1, OUTPUT);
    pinMode(M2, OUTPUT);
    digitalWrite(M0, HIGH);
    digitalWrite(M1, HIGH);
    digitalWrite(M2, HIGH);

    pinMode(LIMIT_SWITCH_PIN, INPUT_PULLUP);

    // Configure steppers
    coneStepper.setEnablePin(CONE_ENABLE_PIN);
    spoutStepper.setEnablePin(SPOUT_ENABLE_PIN);
    
    coneStepper.setMaxSpeed(1000);
    coneStepper.setAcceleration(10000);
    spoutStepper.setMaxSpeed(2000);
    spoutStepper.setAcceleration(10000);
    
    coneStepper.setPinsInverted(false, false, true);
    spoutStepper.setPinsInverted(false, false, true);

    coneStepper.disableOutputs();
    spoutStepper.disableOutputs();

    attach_callbacks();
}

void loop() {
    c.feedinSerialData();

    if (!isQueueEmpty() && !coneStepper.isRunning() && !spoutStepper.isRunning()) {
        Command cmd = dequeueCommand();
        executeCommand(cmd);
    }

    if (coneStepper.isRunning()) {
        coneStepper.enableOutputs();
        coneStepper.run();
    } else {
        coneStepper.disableOutputs();
    }

    if (spoutStepper.isRunning()) {
        spoutStepper.enableOutputs();
        spoutStepper.run();
    } else {
        spoutStepper.disableOutputs();
    }
}

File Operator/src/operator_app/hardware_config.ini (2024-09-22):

[PUMP]
min_flow_rate = 40
forward_pin = 13
reverse_pin = 19

[RELAY_CHANNELS]
channel_1 = 22
channel_2 = 23
channel_3 = 24
channel_4 = 25

[DECAF_API]
decaf_rfid_api_url = https://httpbin.org/post

[SCALES]
cone_scale_data_pin = 17
cone_scale_clock_pin = 27
cone_scale_unit = g
cone_scale_reference_unit = 2085.0
cone_scale_zero_value = 114767.0
mug_scale_data_pin = 5
mug_scale_clock_pin = 6
mug_scale_unit = g
mug_scale_reference_unit = 473.0
mug_scale_zero_value = 97870.0

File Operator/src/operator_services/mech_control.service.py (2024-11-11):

import PyCmdMessenger
import asyncio
import json
import os
import logging
from typing import Any, List, Dict

# Configure logging
logging.basicConfig(level=logging.INFO)
logger = logging.getLogger(__name__)

class MechControlService:
    def __init__(self, socket_path: str = "/tmp/mech-control.sock"):
        # Initialize Arduino
        self.arduino = PyCmdMessenger.ArduinoBoard("/dev/tty.usbserial-11330", baud_rate=9600)
        
        # Command definitions
        self.commands = [
            ["move_cone", "lii"],       # steps, speed, direction
            ["cone_done", ""],
            ["move_spout", "lii"],      # degrees, speed, direction
            ["spout_done", ""],
            ["move_both", "lilii"],     # cone_steps, cone_speed, spout_degrees, spout_speed, direction
            ["both_done", ""],
            ["zero_spout", ""],         # Zero the spout stepper
            ["zero_done", ""],          # Zero complete acknowledgment
            ["error", "s"]
        ]
        
        self.messenger = PyCmdMessenger.CmdMessenger(self.arduino, self.commands)
        self.socket_path = socket_path

    async def wait_for_response(self, expected_done_cmd: str, timeout: float = 30) -> List[Any]:
        loop = asyncio.get_running_loop()
        try:
            while True:
                response = await loop.run_in_executor(None, self.messenger.receive)
                if response is not None:
                    logger.debug(f"Received response: {response}")
                    if response[0] == "error":
                        raise Exception(f"Arduino error: {response[1]}")
                    if response[0] == expected_done_cmd:
                        return response
                await asyncio.sleep(0.1)
        except asyncio.CancelledError:
            raise TimeoutError(f"Timeout waiting for {expected_done_cmd}")

    def validate_command_parameters(self, command: Dict[str, Any]) -> None:
        cmd_type = command.get('command')
        if cmd_type == 'move_cone':
            required_fields = ['steps', 'speed', 'direction']
        elif cmd_type == 'move_spout':
            required_fields = ['degrees', 'speed', 'direction']
        elif cmd_type == 'move_both':
            required_fields = ['cone_steps', 'cone_speed', 'spout_degrees', 'spout_speed', 'direction']
        elif cmd_type == 'zero_spout':
            required_fields = []
        else:
            raise ValueError(f"Unknown command type: {cmd_type}")

        for field in required_fields:
            if field not in command or not isinstance(command[field], int):
                raise ValueError(f"Invalid or missing '{field}' in command.")

    async def execute_command(self, command: Dict[str, Any]) -> List[Any]:
        cmd_type = command.get('command')
        loop = asyncio.get_running_loop()
        self.validate_command_parameters(command)

        try:
            if cmd_type == 'zero_spout':
                await loop.run_in_executor(None, self.messenger.send, 'zero_spout')
                logger.info(f"Sent command: zero_spout")
                response = await asyncio.wait_for(self.wait_for_response('zero_done'), timeout=30)

            elif cmd_type == 'move_cone':
                steps = command['steps']
                speed = command['speed']
                direction = command['direction']
                await loop.run_in_executor(None, self.messenger.send, 'move_cone', steps, speed, direction)
                logger.info(f"Sent command: move_cone with steps={steps}, speed={speed}, direction={direction}")
                response = await asyncio.wait_for(self.wait_for_response('cone_done'), timeout=30)

            elif cmd_type == 'move_spout':
                degrees = command['degrees']
                speed = command['speed']
                direction = command['direction']
                await loop.run_in_executor(None, self.messenger.send, 'move_spout', degrees, speed, direction)
                logger.info(f"Sent command: move_spout with degrees={degrees}, speed={speed}, direction={direction}")
                response = await asyncio.wait_for(self.wait_for_response('spout_done'), timeout=30)

            elif cmd_type == 'move_both':
                cone_steps = command['cone_steps']
                cone_speed = command['cone_speed']
                spout_degrees = command['spout_degrees']
                spout_speed = command['spout_speed']
                direction = command['direction']
                await loop.run_in_executor(
                    None,
                    self.messenger.send,
                    'move_both',
                    cone_steps,
                    cone_speed,
                    spout_degrees,
                    spout_speed,
                    direction
                )
                logger.info(f"Sent command: move_both with cone_steps={cone_steps}, cone_speed={cone_speed}, "
                            f"spout_degrees={spout_degrees}, spout_speed={spout_speed}, direction={direction}")
                response = await asyncio.wait_for(self.wait_for_response('both_done'), timeout=30)

            else:
                raise ValueError(f"Unknown command type: {cmd_type}")

            return response

        except Exception as e:
            logger.error(f"Error executing command {cmd_type}: {str(e)}", exc_info=True)
            return ['error', str(e)]

    async def handle_client(self, reader: asyncio.StreamReader, writer: asyncio.StreamWriter) -> None:
        while True:
            try:
                data = await reader.readline()
                if not data:
                    break

                received_data = json.loads(data.decode())
                responses = []

                if isinstance(received_data, list):
                    # Handle array of commands
                    for command in received_data:
                        response = await self.execute_command(command)
                        responses.append({
                            'command': command['command'],
                            'status': response[0] if response else 'no_response',
                            'data': response[1] if response and len(response) > 1 else None
                        })
                else:
                    # Handle single command
                    response = await self.execute_command(received_data)
                    responses.append({
                        'command': received_data['command'],
                        'status': response[0] if response else 'no_response',
                        'data': response[1] if response and len(response) > 1 else None
                    })

                # Send response back to client
                writer.write((json.dumps(responses) + '\n').encode())
                await writer.drain()
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

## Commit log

2018-03-19 Initial Cad Upload
    [pourOverMount.stl, sweepServoMount.stl, waterSweepV1.stl]
2018-06-16 Ino zip commit
    Ino provides CLI Arduino control over USB/Serial
2018-06-16 relayContol.py commit
    relayContol.py is a basic testing script to run through Mugsy's relay breakout board.
2018-06-23 Create pinRelayTester.ino
    Basic digital pin tester
    Wiring: Connect digital pin 12 to the S pin on relay
    Connect 3V3 pin to + pin on relay
    Connect GND pin to - pin on relay
2018-08-11 initial commit
    First test of a stacking controller/breakout mounting plate. Individual plates will be separated by m3 stand offs.
    [controllerPlates.stl]
2018-08-11 Add files via upload
    Added footprints for Pi, L2989 Module, 4x Relay Module
    [controllerPlates.stl]
2018-08-14 Add files via upload
    Updated plate. Fixed relay footprint.
    [controllerPlates.stl]
2018-08-14 Add files via upload
    RGB LED Mount for 15mm Extrusion
    [rgbLedMount.stl]
2018-08-25 Add files via upload
    Secures touchscreen to front acrylic panel.
    [screenClipV2.stl]
2018-08-25 Add files via upload
    Updated hole placement.
2018-09-24 STL Updates
    Final controller plate version: Redesigned to be much more basic, now able to be laser cut in addition to 3d printable
    Initial update of Pour Over Mechanism Mid Section for V3 set up.
    [PouroverMidSection.stl, controllerPlates.stl]
2018-09-27 Pour over mechanism lid(laser cut)
    [pourOverMechTop.dxf]
2018-10-17 initial commit
    Status: Working. This script reads the boiler temperature, converts that value to an RGB value,
    sends it to the LEDs and then sends the temp over serial to the Pi
    TODO Need to add comments, clean up old pattern references and any other left over code from base file
    This code is just a hacked version of the FastLED DemoReel100 by Mark Kriegsman.
2018-11-09 More STL uploads
    [barcodeScanMount.stl, coneMechGear.stl, coneMechGearTop.stl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]
2018-11-21 Add files via upload
    controllerPlatesLaser.dxf Laser file for controller plates
    behindScreenDividerLaser.dxf Laser file for the divider which separates the screen electronics from the coffee making bits.
    [behindScreenDividerLaser.dxf, controllerPlatesLaser.dxf]
2019-01-20 Grinder spout and mount upload
    [grinderSpoutMountV2.stl, grinderSpoutV2.stl]
2019-01-26 Create coneStepperSerialControl.ino
    //need to switch AccelStepper lib as well as integrate into the larger runtime.
    //200 steps = one rotation of stepper, 1600 steps = one rotation of pour over cone
    //commands can be chained
    //format = <CW,1600,60.00> (Direction, Steps, Speed)
    //Chained example: <CW,800,60.00><CC,800,60.00><CW,800,60.00><CC,1600,60.00><CW,1600,60.00>
2019-01-28 Updated to hold second L298N for water pumps
    [controllerPlates.stl, controllerPlatesLaser.dxf]
2019-02-14 Add files via upload
    New internal plug cap to protect contacts.
    [plugCap.stl]
2019-03-21 Mag Connector Upload
    [magConnLid.2.stl, magConnMachineSide.2.stl, magConnPanelSide.2.stl]
2019-03-29 Add files via upload
    V4 Panel Mount
    [panelMagnetMount.V4.stl]
2019-06-14 Non Blocking Serial Motor Control: bugs
    Conversion to non blocking has introduced some bugs, namely command chaining is broken. Fix in progress.
2019-06-14 Fixed Seria Command Chaining
2019-06-15 added additional command for relay control
2019-06-22 Create mugsyCommander.ino
    Need to add back water timings and dual4 temp sensors
2019-07-15 Add files via upload
    Almost complete CAD model for entire Mugsy. Still need to add remaining electronics, boiler, grinder and hopper as well as link the assemblies properly. 99% of the structural parts are in there thoug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
2019-08-20 Fixed incorrect hole size due to export error
    [mugsyBaseSidePanel.dxf]
2019-08-20 base side panels for extensions, 210 and 270mm
    [mugsyBaseSidePanel_210mm.dxf, mugsyBaseSidePanel_270mm.dxf]
2019-08-31 Create brewing.php
    Need to put timer back in after refactoring. Also need to create a new css class for list items and remove inline css.
2019-09-01 Update brewing.php
    Added the step timer display js back in. Still need to link progress bar to timer and put function in it's own js file.
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2019-11-11 Add in second temp sensor and return average
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2019-11-13 Create integrations.php
    Need to link revocation button to confirmation and db. Also need to make bootstrap table js a local resource along with moving some inline css.
2019-11-28 base recipe builder frame
    Lots to add back in, main js, form types and db conn. Also need to pull inline css.
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2020-01-02 belt route sketch
    [mugsyBelt.dxf]
2020-06-11 Updated version of the RFID Mount
    [rfidMount_V3.stl]
2020-06-16 Front Panel Rotary Encoder Breakout Mount
    [rotaryEncoderMount.stl]
2020-06-16 Option mount for barcode scanner servo control
    [scannerServoMount(optional).stl]
2021-05-10 Update to use drv8825 type step motor controller
2021-05-11 Offset mount for LED PCB (enclosure lighting)
    [lightBarMount_V2.stl]
2021-05-11 Add Eagle files for Mugsy lightBar
    [lightBarV2_a.brd, lightBarV2_a.sch]
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2021-05-28 add PCB files for v.08 controller
    [mugsyBrainBoard_p08.brd, mugsyBrainBoard_p08.sch]
2021-12-06 Add cup sensor mount stl.
    The cup sensor makes sure Mugsy only brews when a mug is present.
    [mugSensorMount_partA.stl]
2021-12-23 Rear enclosure lightbar mounts
    These mounts allow you to place the lightbar at the rear of the enclosure when you have a front panel color other than white. It will throw the LED visualizations against the wall behind the unit.
    [lightbarMountRear.stl]
2024-09-22 Reset repository, begin refactor to Mugsy monorepo for all services
    [PouroverMidSection.stl, barcodeScanMount.stl, behindScreenDividerLaser.dxf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]

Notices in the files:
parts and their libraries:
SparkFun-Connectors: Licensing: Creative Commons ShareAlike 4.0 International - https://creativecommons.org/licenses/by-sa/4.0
